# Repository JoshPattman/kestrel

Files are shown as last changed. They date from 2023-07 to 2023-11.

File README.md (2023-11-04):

# Kestrel - A 3D printable 1:14th RC car

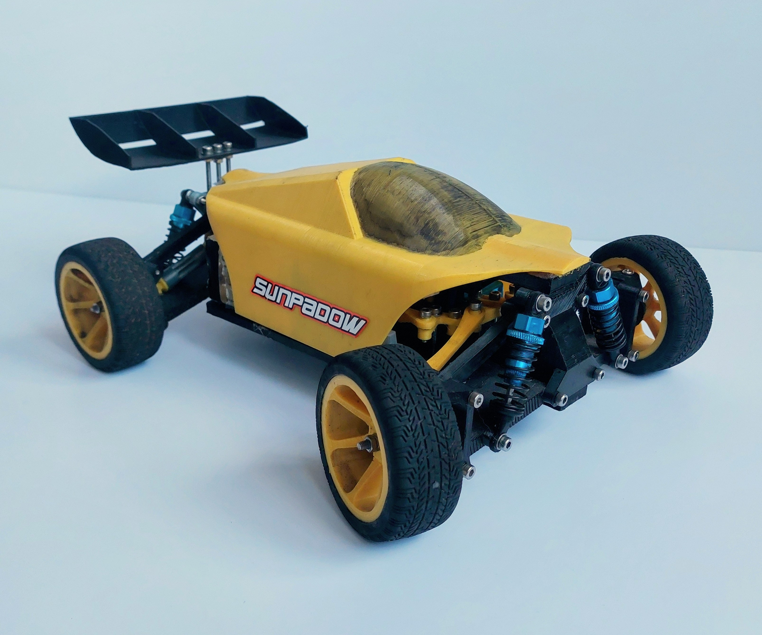
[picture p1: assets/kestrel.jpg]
cover image

 
This is the repo for the design files for my 3D printable RC buggy, the Kestrel. The primary goal was to make the Kestrel fun to drive in a lot of situations, so it is not particularly good for racing, bashing, or drifting, but it can do a bit of each. I also wanted to design the Kestrel to be smaller than many other 3D printed buggies, so it is roughly 1:14 scale. Here are some of the features:
- Rear-wheel drive using a belt
- No differential (this enables the car to be simpler and more robust)
- Uses oil-filled adjustable shocks
- Fits rubber tyres
- Can be used with TPU drive axles for higher durability

## Parts List
Here are the parts that you need to build this car:

### Materials
- ~400g of filament - I used ESUN PLA+ for every part of the print
- Small amount of TPU (Optional-ish) - Used only for the drive shafts but drastically improves drivetrain durability
- 12x `6700-2RS` bearings
- 4x 60mm RC car shocks - Ensure that both ends of the shock have an open hole and not a ball joint
- 4x RC car tyres - I used 1:10 touring car tyres which can be found [here](https://www.amazon.co.uk/gp/product/B0BHDSPXZH/ref=ox_sc_act_title_1?smid=A1N8E4Q081571L&psc=1). If you want to use different tyres it should be straightforward to modify the wheel file to fit them.
- 6mm wide 2GT/GT2 circular belt with a length of about 160mm - I have successfully used a belt that I spliced to the correct size.
- Sticky velcro
- Some sort of grease to reduce friction between 3d printed gears - I am using bike grease
- A set of M3 bolts and nuts of varying lengths
- Superglue/Glue gun

### Electronics
- `MG90S` servo
- `EMAX 2213` motor
- 2S/3S LiPo battery - I am using 3S
- ESC
- Receiver
- Gyro (Optional) - I have found that due to the locked diff, the car really likes to spin out. I am also not a very good driver though, so you might not need this.

## Build instructions
I am working on making a video showing how to build the car. I will link it here when I am done.

## CAD
For this project I am using [FreeCAD Link Branch 2023-01-31](https://github.com/realthunder/FreeCAD/releases/tag/2023.01.31-edge). You can try it out with a different version of FreeCAD, but it may break.

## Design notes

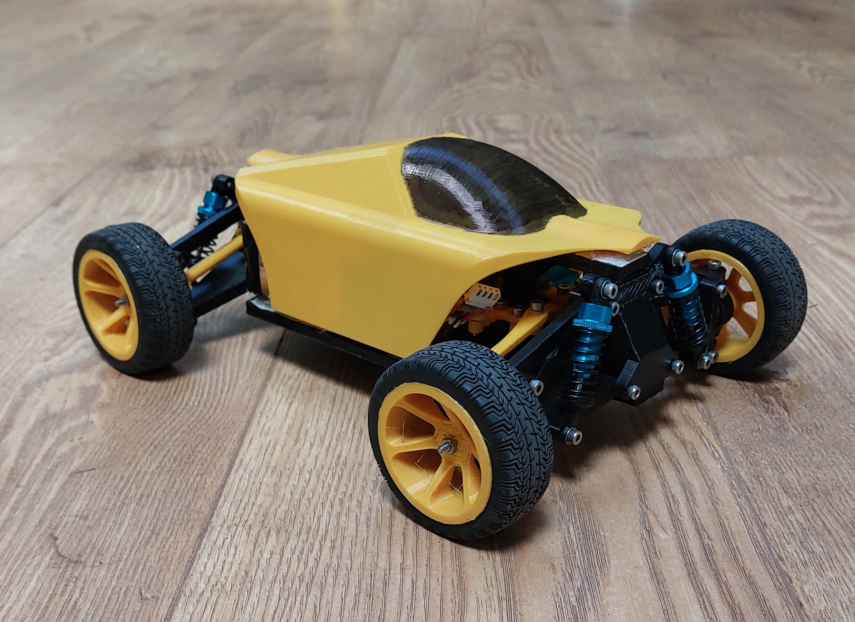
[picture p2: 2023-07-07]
assets/kestrel2.jpg

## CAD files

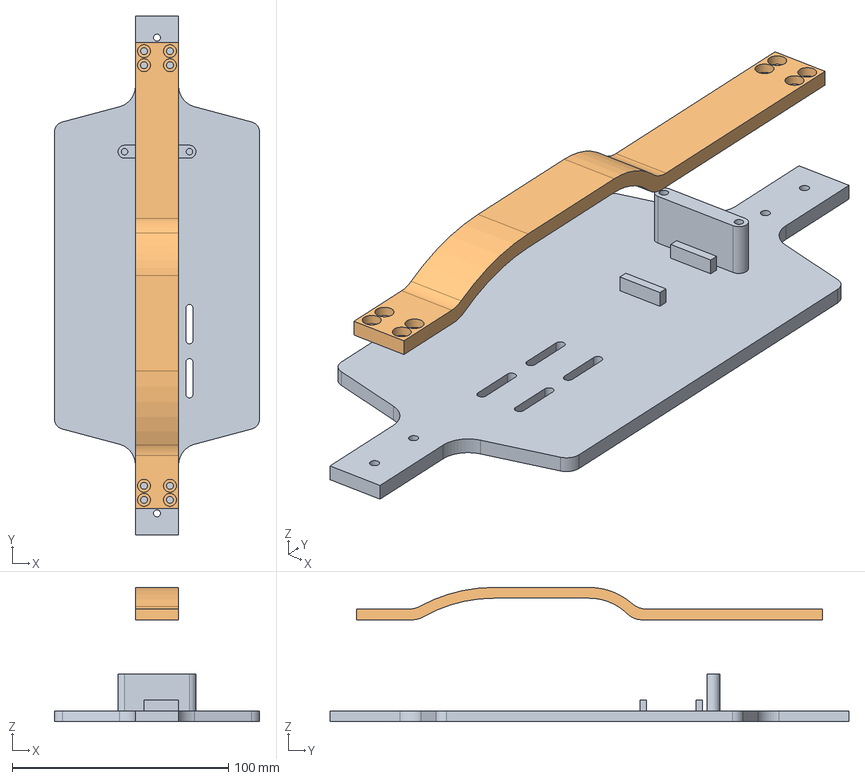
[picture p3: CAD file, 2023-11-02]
cad/body_v3.FCStd
95.0 x 240.0 x 62.0 mm
strengthener_bar

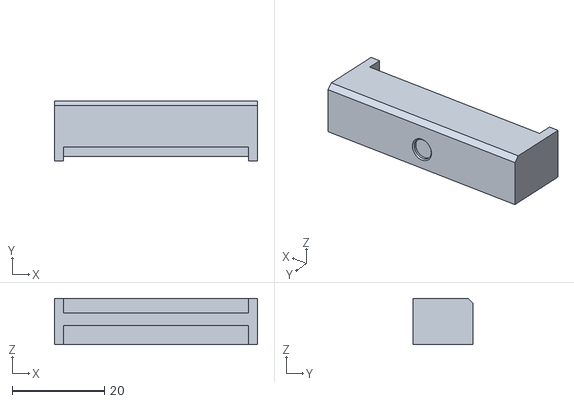
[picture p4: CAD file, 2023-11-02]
stl/gearbox_v2-tensioner_plate.stl
44.0 x 13.0 x 10.0

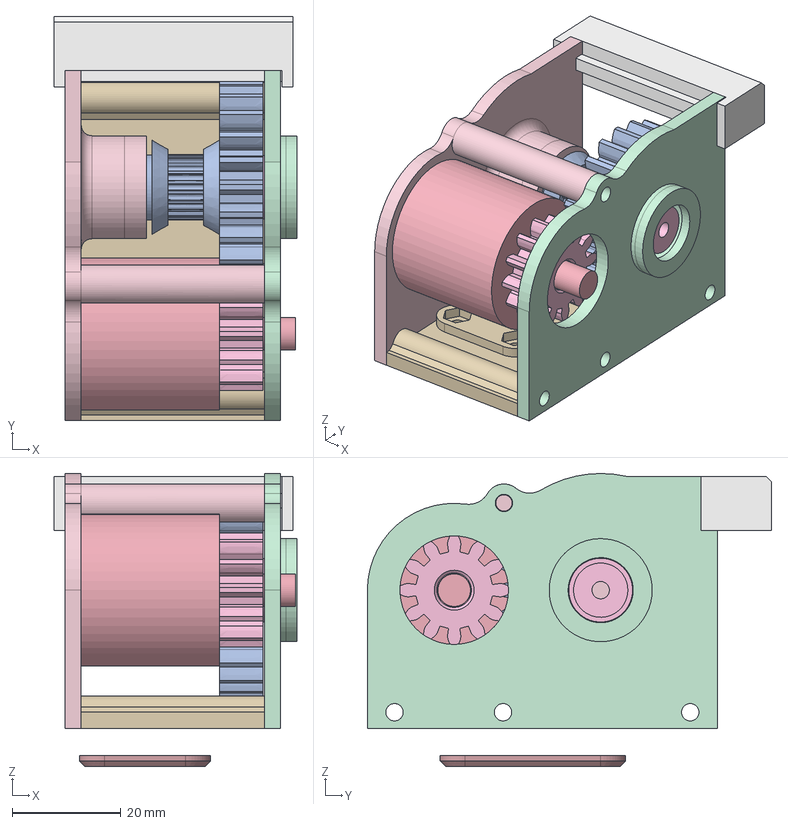
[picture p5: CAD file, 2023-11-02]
cad/gearbox_v2.FCStd
44.8 x 74.5 x 54.0 mm
pulley
pinion
motor
right_plate
left_plate
bottom_plate
bearing_plug
lower_clamp
tensioner_plate

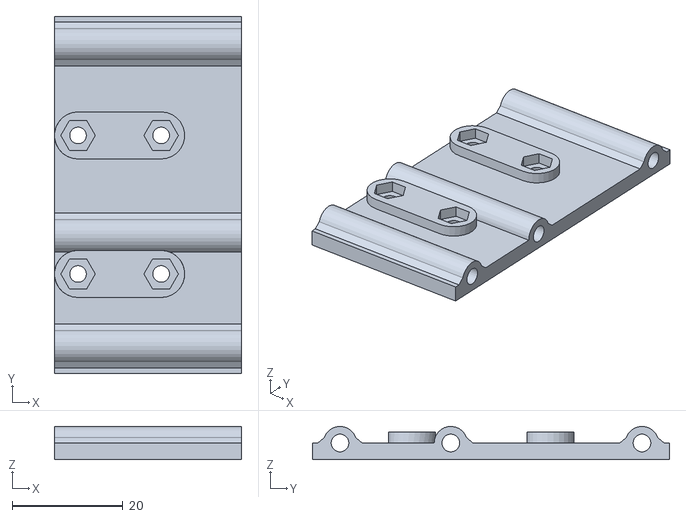
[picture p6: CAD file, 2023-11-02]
stl/gearbox_v2-bottom_plate.stl
33.8 x 64.5 x 6.00

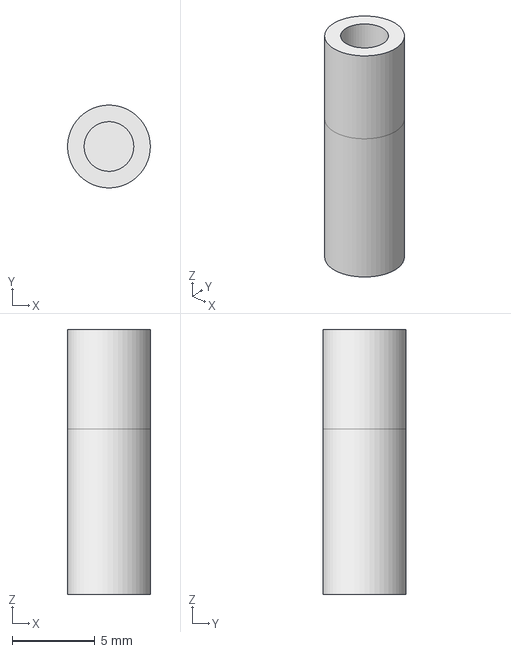
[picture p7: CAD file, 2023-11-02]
cad/tensioner_cap.FCStd
5.00 x 5.00 x 16.0 mm

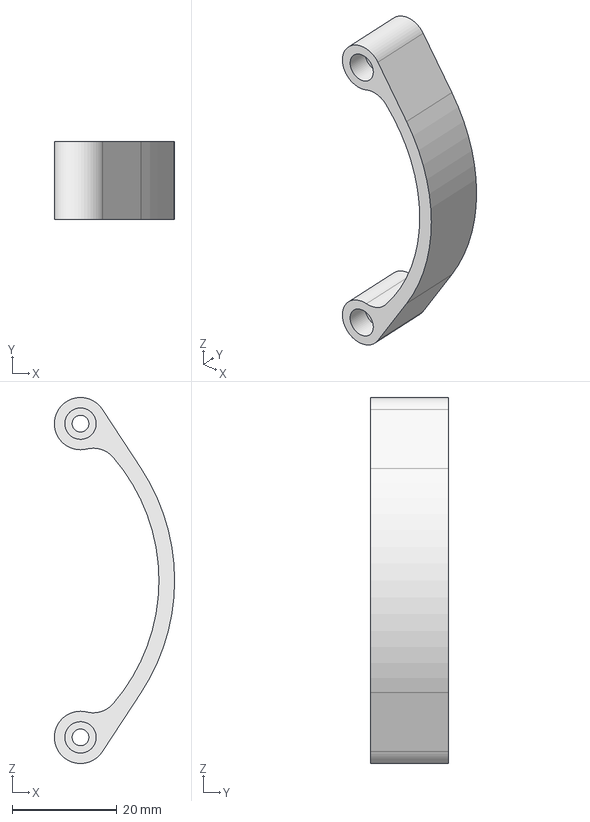
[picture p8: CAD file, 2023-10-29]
cad/tpu_suspension.FCStd
23.0 x 15.0 x 70.0 mm

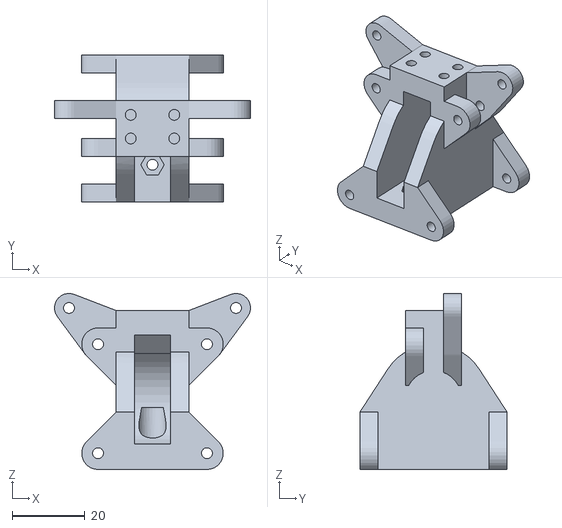
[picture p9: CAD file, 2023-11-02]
stl/drive_components-tower_front.stl
54.0 x 40.5 x 48.5

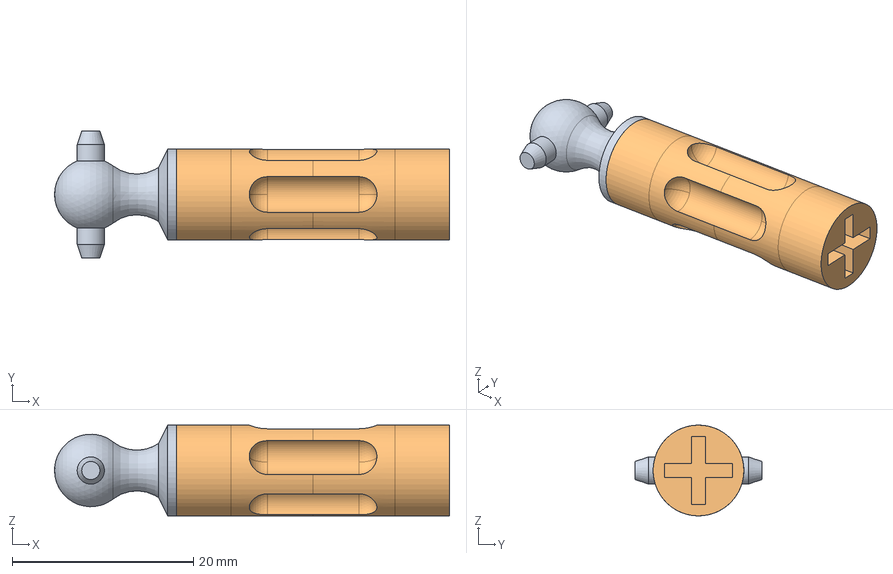
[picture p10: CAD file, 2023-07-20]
cad/tpu_drive_shaft.FCStd
43.5 x 14.0 x 10.0 mm
shaft_end
torque_damper

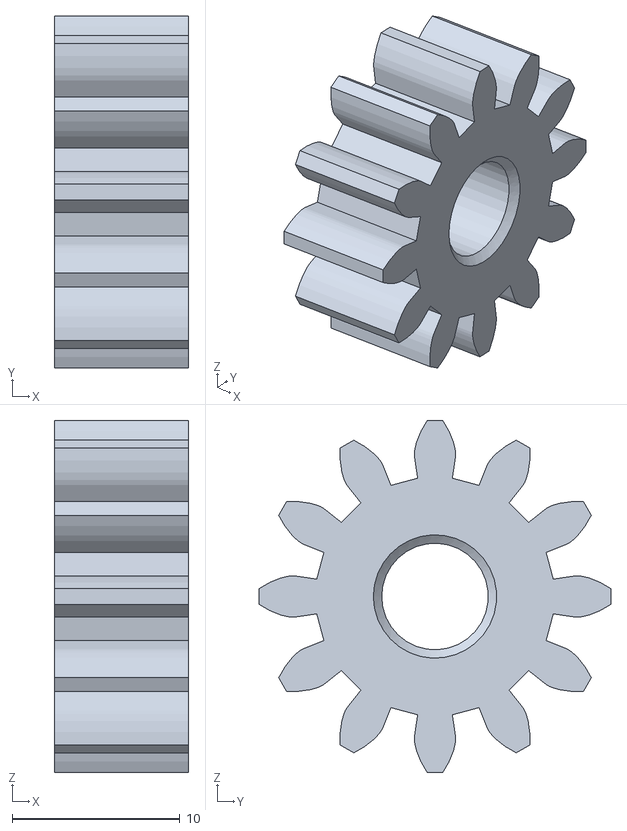
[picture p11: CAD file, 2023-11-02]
stl/gearbox_v2-pinion.stl
8.00 x 21.0 x 21.0

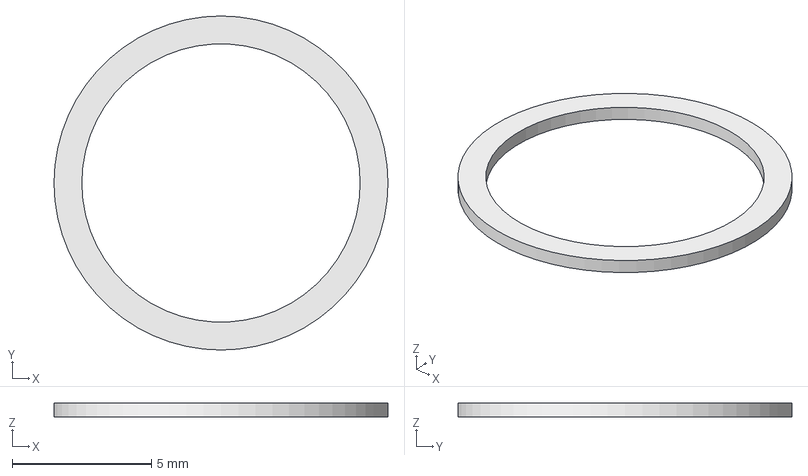
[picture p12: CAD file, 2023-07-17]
cad/bearing_spacer.FCStd
12.0 x 12.0 x 0.5 mm

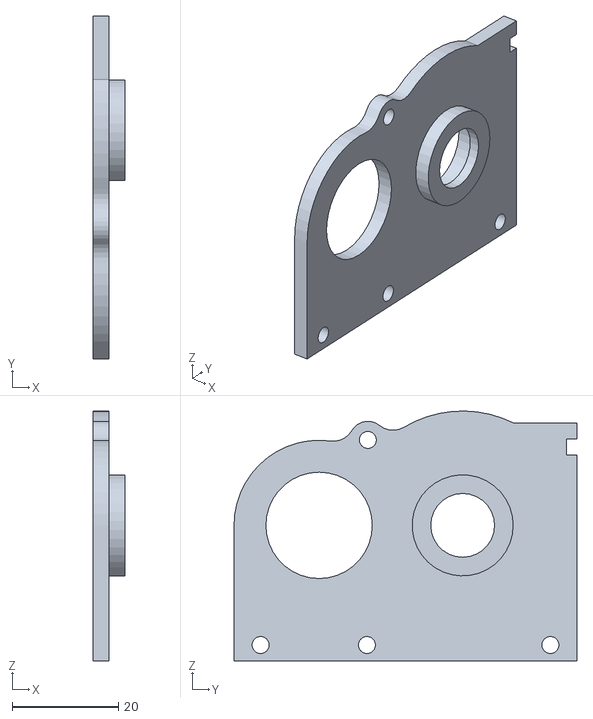
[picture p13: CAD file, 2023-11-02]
stl/gearbox_v2-right_plate.stl
6.00 x 64.5 x 47.0

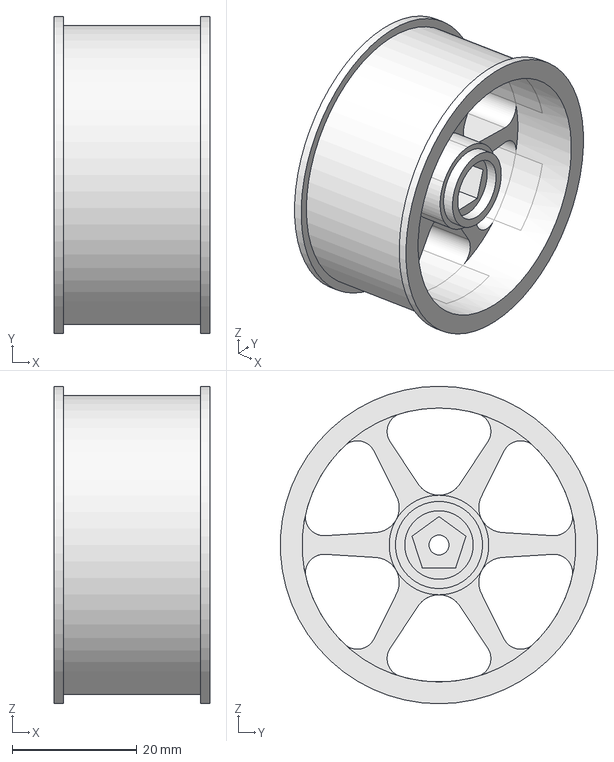
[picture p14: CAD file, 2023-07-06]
cad/wheel.FCStd
25.0 x 50.9 x 51.0 mm

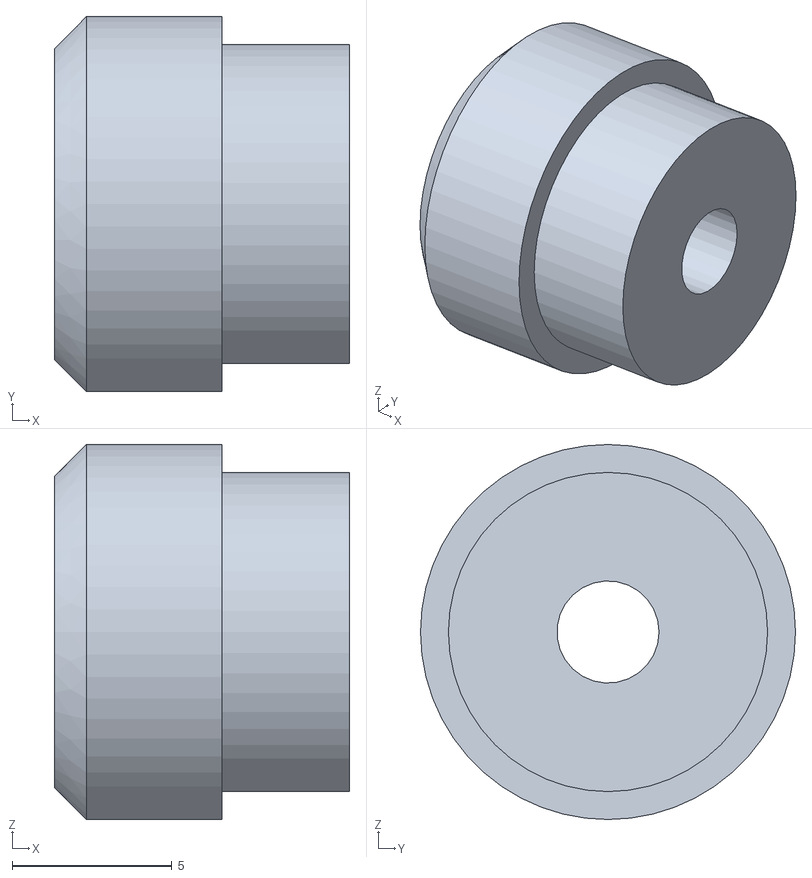
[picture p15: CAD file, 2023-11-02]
stl/gearbox_v2-bearing_plug.stl
9.25 x 11.8 x 11.8

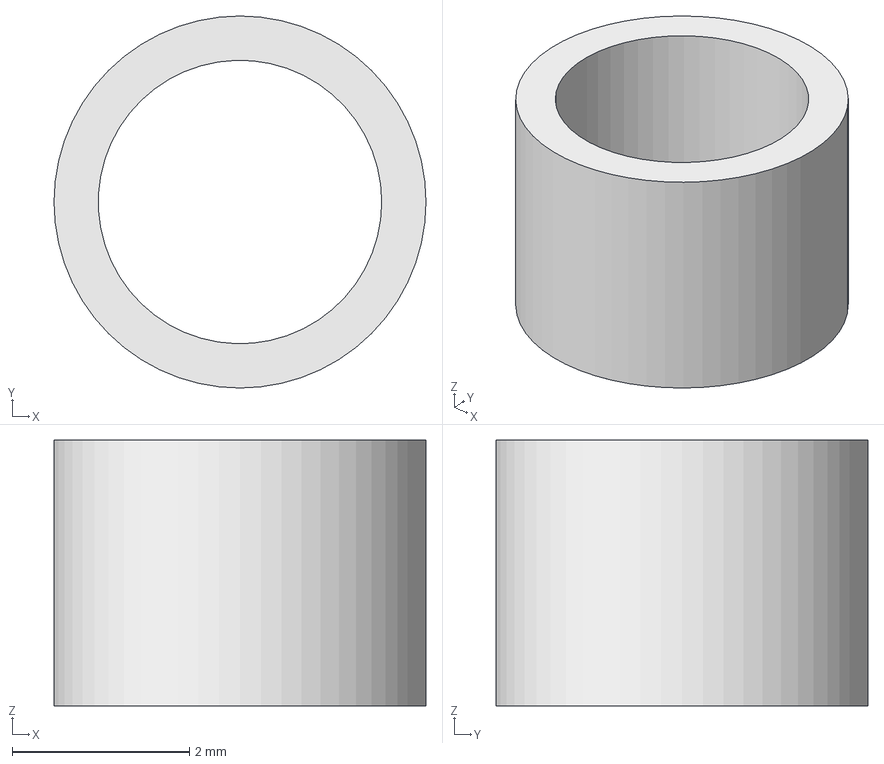
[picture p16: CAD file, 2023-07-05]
cad/shock-spacers.FCStd
4.20 x 4.20 x 3.00 mm

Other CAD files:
stl/tensioner_cap-tc.stl
stl/gearbox_v2-left_plate.stl
stl/drive_components-tower_rear.stl
stl/gearbox_v2-lower_clamp.stl
stl/bearing_spacer-spacer.stl
stl/body_v3-body.stl
stl/body_v3-shell.stl
stl/body_v3-strengthener_bar.stl
stl/drive_components-belt_gear.stl
stl/drive_components-drive_shaft.stl
stl/drive_components-lower_arm.stl
stl/drive_components-lower_cup.stl
stl/drive_components-power_knuckle.stl
stl/drive_components-servo_linkage_arm_v2.stl
stl/drive_components-servo_saver_v2.stl
stl/drive_components-spoiler.stl
stl/drive_components-steering_clamp.stl
stl/drive_components-steering_i_pivot.stl
stl/drive_components-steering_knuckle.stl
stl/drive_components-steering_l_pivot.stl
stl/drive_components-steering_linkage.stl
stl/drive_components-steering_linkage_arm.stl
stl/drive_components-tower.stl
stl/drive_components-tower_spoiler.stl
stl/drive_components-turny_bit.stl
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

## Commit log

2023-07-05 Initial Commit with version 1
    [body_v2.FCStd, body_v3-body.stl, body_v3-shell.stl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]
2023-07-05 Removed unused files
    [body_v2.FCStd, bumper.FCStd]
2023-07-05 Added instructions for CAD
2023-07-06 Added more space around the cup bearings and changed pentagon size
    [drive_components-belt_gear.stl, drive_components-lower_cup.stl, drive_components-steering_clamp.stl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]
2023-07-07 Thickened Turny Bit as one of them on my car broke
    [drive_components-turny_bit.stl]
2023-07-07 removed unused tensioner and thickened arms
    [body_v3-body.stl, body_v3-strengthener_bar.stl, body_v3.FCStd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]
2023-07-16 update fixed diff so now you can tighten it al the way without it getting too tight
    [drive_components-belt_gear.stl, drive_components-upper_cup.stl]
2023-07-17 Added a new file for a tpu damped drive shaft
    [tpu_drive_shaft.FCStd]
2023-07-17 TPU driveshaft and spacer
    [bearing_spacer-spacer.stl, bearing_spacer.FCStd, drive_components-servo_linkage_arm_v2.stl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]
2023-07-20 tpu drive shaft works but cant print properly
    [drive_components-power_knuckle.stl, tpu_drive_shaft-shaft_end.stl, tpu_drive_shaft-torque_damper.stl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]
2023-10-27 Changed gear ratio
    [gearbox_v2-bearing_plug.stl, gearbox_v2-bottom_plate.stl, gearbox_v2-left_plate.stl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]
2023-10-27 Added a spoiler
    [drive_components-spoiler.stl, drive_components-tower_spoiler.stl, gearbox_v2.FCStd]
2023-10-29 Larger Spoiler
    [drive_components-spoiler.stl]
2023-10-30 Added areas to put tensioner
    [body_v3.FCStd, drive_components-tower_front.stl, drive_components-tower_rear.stl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]
2023-10-30 beefed up the arm linkage
    [drive_components-tower_front.stl, drive_components-tower_rear.stl, gearbox_v2.FCStd]
2023-10-31 Better tensioner plate
    [gearbox_v2-tensioner_plate.stl, gearbox_v2.FCStd, tensioner_cap-tc.stl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]
2023-11-02 Added an axle to pulley in gearbox to make it stronger
    [gearbox_v2-bearing_plug.stl, gearbox_v2-pulley.stl, gearbox_v2.FCStd]
